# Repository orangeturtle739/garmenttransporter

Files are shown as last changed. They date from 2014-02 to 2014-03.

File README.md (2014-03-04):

garmenttransporter
==================
This project is my entry for the Hack the Arduino Robot competition (http://www.robotchallenge.org/competition/).

In June 2012, I build an automatic shirt-folding robot. In January 2014, I entered the Hack the Arduino Robot competition (http://www.robotchallenge.org/competition/) to try and win a free Arduino Robot. For the competition, I submitted the following paragraph describing what I would do if I won the robot:
“A couple of years ago, I built an Arduino-powered shirt-folding machine which folds clothes. Using the Arduino robot from the RobotChallenge, I will build a device to remove folded clothes from the machine and to stack them. My idea is special because it will involve two Arduinos (the Arduino Uno in the shirt folder, and the Arduino robot) which will have to communicate, and because it will be very useful. The robot will solve the real life problem of laundry folding by making the task easier and faster and by doing so nicely; the robot will use a custom-designed gripper to transport garments while keeping them perfectly folded.”
I won the robot and am now implementing my project.

The purpose of the project is to create an automatic shirt-stacking robot to go with the automatic shirt folding robot that I already have. The shirt stacking robot picks up a shirt from the shirt folder and then places the shirt into a pile.

This git repository contains all of my files for both the original shirt-folding robot along with the files for the shirt-stacking robot.

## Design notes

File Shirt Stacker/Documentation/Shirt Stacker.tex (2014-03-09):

\documentclass[12pt,letterpaper]{article}
\usepackage[utf8]{inputenc}
\usepackage{amsmath}
\usepackage{amsfonts}
\usepackage{amssymb}
\usepackage{graphicx}
\usepackage{hyperref}
\usepackage[space]{grffile}
\graphicspath{{/Users/jacob/Documents/My Stuff/Arduino/garmenttransporter/Shirt Stacker/Design/Images/}}

\title{Shirt Stacker}
\author{}
\date{}

\begin{document}
\maketitle
\section{Introduction}
This document describes the shirt-stacking machine which I built. The shirt-stacking machine is capable of picking up shirts from my shirt folder and stacking them. The machine is controlled by an Arduino Robot. All files for the shirt stacker can be found at \url{https://github.com/orangeturtle739/garmenttransporter/tree/master/Shirt\%20Stacker}.

\section{Design}
The shirt stacker consists of a rotating turntable and a spatula. The stacker picks up the shirt on the spatula, rotates and then drops the shirt. The spatula moves up and down using linear bearings. Figure \ref{topview} shows a rendering of the shirt stacker.

A SketchUp model of the shirt folder can be found at \url{https://github.com/orangeturtle739/garmenttransporter/blob/master/Shirt\%20Stacker/Design/Actual%20Design.skp}.

\subsection{Mechanics}
\subsubsection{Rotating}
The rotation is powered by the Arduino Robot's left wheel. The wheel rotates on a rubber track to rotate the shirt stacker. The turntable itself rotates on a lazy susan bearing. The Arduino Robot is attached to the rotating section with a wooden arm. Fiqure \ref{crossection} shows the mechanics.

\subsubsection{Lifting}
The lifting is powered by the Arduino Robot's right wheel. The wheel is attached to a wooden dowel which is attached to a string. When the wheel turns, the string winds up on the dowel. The spool and wheel connection are shown in figure \ref{spool}. The string then passes through a setup consisting of 9 pulleys. The pulleys are visible in figure \ref{pulleys}. This setup lifts the carriage that contains the spatula.

The carriage moves up and down on two linear bearings. Figure \ref{linearbearings} shows the bearings.

\subsubsection{Dumping}
Once the shirt folder has lifted the shirt and rotated to the proper location, the shirt folder drops the shirt. It does this by rotating the spatula. The spatula is attached to a wooden dowel which goes through a bearing. Along the diameter of the flat side of the dowel sticking out of the bearing, there are two nails, both very close to the edge. Figure \ref{nails} shows the location of the nails. Both nails are a attached to a piece of elastic to make the spatula self-righting. One nail is a attached to a string. The other end of the string is tied onto a screw eye on the base of the rotating platform. When the spatula reaches a specific height, this piece of string causes it to rotate. Once the robot lowers the spatula, the elastic makes it level again. This is shown in figure \ref{dumping}.

\section{Parts}
For the lazy susan bearing, I used this part: \url{http://www.amazon.com/gp/product/B00004YOKA/ref=oh_details_o02_s01_i03?ie=UTF8&psc=1}. For the linear bearings, I used these bearings: \url{http://www.amazon.com/gp/product/B00CGR8WUU/ref=oh_details_o03_s00_i01?ie=UTF8&psc=1}. I put the bearings on these shafts: \url{http://www.amazon.com/gp/product/B002BBJ0CA/ref=oh_details_o02_s00_i01?ie=UTF8&psc=1}. I held the shafts in place with these parts: \url{http://www.amazon.com/gp/product/B00C4PBMMY/ref=oh_details_o03_s00_i00?ie=UTF8&psc=1}.

\section{Use}
To use the shirt stacker, install the program which can be found at \url{https://github.com/orangeturtle739/garmenttransporter/blob/master/Shirt\%20Stacker/Code/Code.ino}. After installing the program, turn the Arduino Robot on. Use the Arduino Robot's buttons to control where the shirt stacker will place the shirt. After a button has been pressed, the robot will wait 14 seconds. Then, it will lift the shirt, rotate and then drop the shirt. 

\begin{figure}[ht]
  \centering
    
    \caption{Top view of shirt stacker.}
    \label{topview}
\end{figure}
\begin{figure}[ht]
  \centering
    
    \caption{Cross-sectional view of the shirt stacker.}
    \label{crossection}
\end{figure}
\begin{figure}[ht]
  \centering
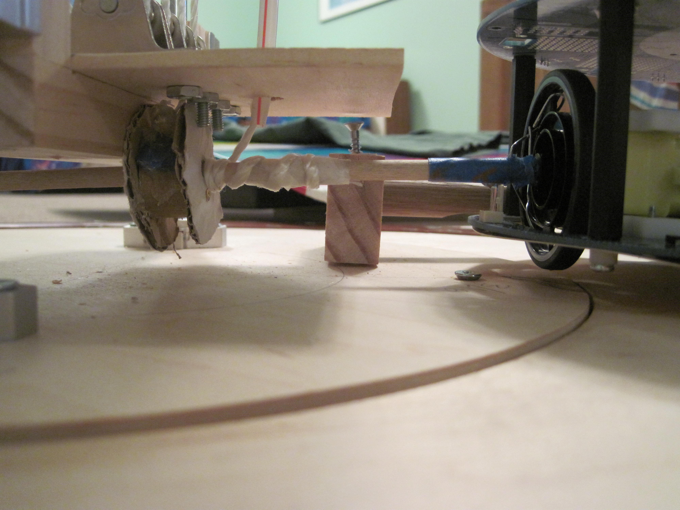
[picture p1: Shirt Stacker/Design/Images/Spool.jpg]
    
    \caption{The spool connected to the right wheel.}
    \label{spool}
\end{figure}
\begin{figure}[ht]
  \centering
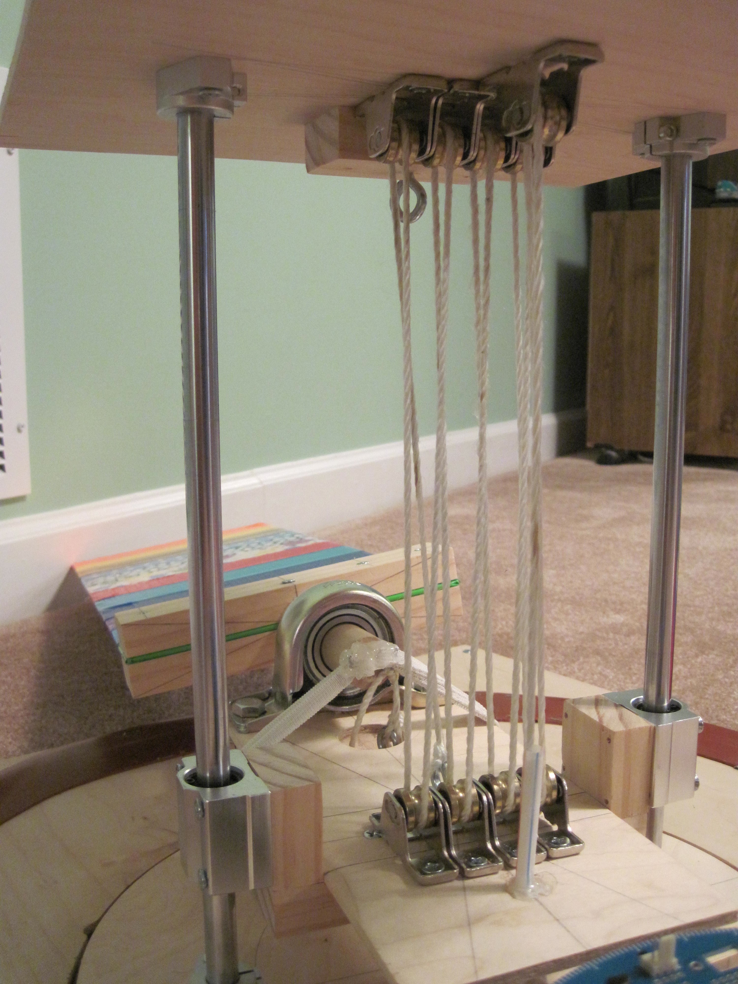
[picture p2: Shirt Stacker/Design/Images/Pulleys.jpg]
    
    \caption{The pulleys on the shirt stacker.}
    \label{pulleys}
\end{figure}
\begin{figure}[ht]
  \centering
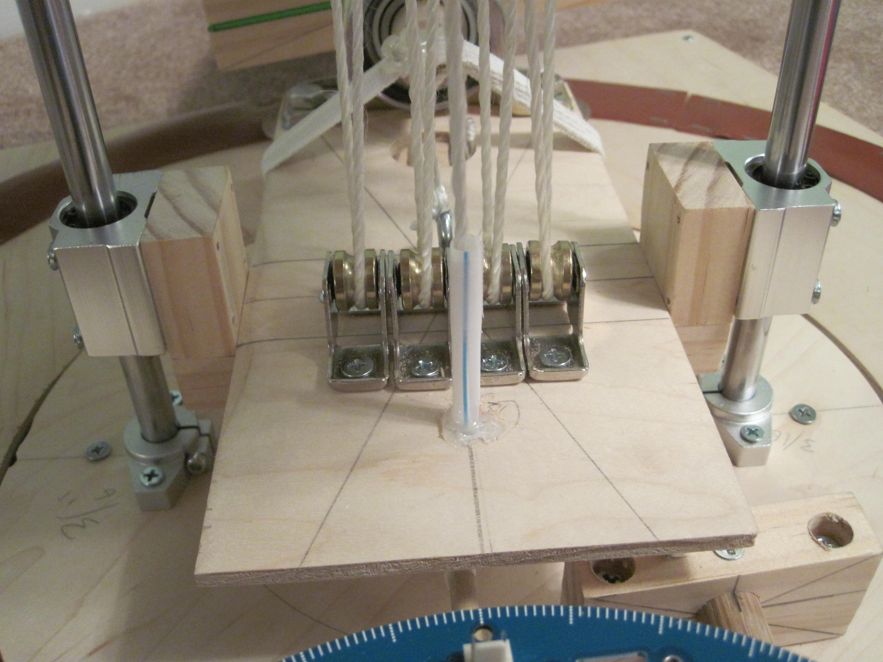
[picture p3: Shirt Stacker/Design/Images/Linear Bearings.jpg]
    
    \caption{The linear bearings.}
    \label{linearbearings}
\end{figure}
\begin{figure}[ht]
  \centering
    
    \caption{The location of the nails in the end of the dowel.}
    \label{nails}
\end{figure}
\begin{figure}[ht]
  \centering
3    
    \caption{The dumping mechanics.}
    \label{dumping}
\end{figure}
\end{document}

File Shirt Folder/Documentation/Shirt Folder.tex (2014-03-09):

\documentclass[12pt,letterpaper]{article}
\usepackage[utf8]{inputenc}
\usepackage{amsmath}
\usepackage{amsfonts}
\usepackage{amssymb}
\usepackage{graphicx}
\usepackage{hyperref}
\usepackage[space]{grffile}
\graphicspath{{/Users/jacob/Documents/My Stuff/Arduino/Shirt Folder/Shirt Folder/Design/Images/}}

\title{Shirt Folder}
\author{}
\date{}

\begin{document}
\maketitle
\section{Introduction}
This document describes the shirt-folding machine which I built. The shirt-folding machine is capable of folding most garments including shirts, shorts and pants. All files for the shirt folder can be found at \url{https://github.com/orangeturtle739/garmenttransporter/tree/master/Shirt\%20Folder}.

\section{Design}
The shirt folder consists of three flaps. Each flap is connected to a servo which can rotate the flap. Figure \ref{topview} shows a rendering of the shirt folder. Each of the flaps fold inward as shown in figure \ref{opentopview}.

The servos are connected to the flaps with a linkage consisting of wooden arms. Figure \ref{servolinkage} shows the linkage. When the button is hit, the shirt folder folds a shirt.

A SketchUp model of the shirt folder can be found at \url{https://github.com/orangeturtle739/garmenttransporter/blob/master/Shirt\%20Folder/Design/Shirt\%20Folder.skp}.

\section{Electronics}
Figure \ref{schematic} shows a schematic of the shirt folder's circuit. Every servo has its own 6V power supply and the Arduino Uno has a 9V power supply. All of the power supplies have their own switches and all of the grounds are connected together.

\section{Parts}
I used TowerPro 9805BB servos because they are able to provide lots of torque. For the main switch (labeled "Button" in figure \ref{topview}), I used a round push-on/push-off switch. For the Arduino switch and the servo switches, I used rocker switches.

\section{Use}
To use to shirt folder, install the program which can be found at \url{https://github.com/orangeturtle739/garmenttransporter/blob/master/Shirt\%20Folder/Shirt_Folder/Shirt_Folder.ino}. After installing the program, turn the Arduino on. Press the main switch twice (turn it on then off again) to initialize the servos. Then, place the shirt onto the shirt folder and press the main switch. Once the bottom flap has be activated, the folder will wait. Pull the shirt onto the bottom flap and press the main switch again. This will cause the bottom flap to rotate one more time which will complete the shirt folding.

\begin{figure}[ht]
  \centering
    
    \caption{Top view of shirt folder.}
    \label{topview}
\end{figure}
\begin{figure}[ht]
  \centering
    
    \caption{Top view of shirt folder with one of the side flaps rotated.}
    \label{opentopview}
\end{figure}
\begin{figure}[ht]
  \centering
    
    \caption{The servo linkage.}
    \label{servolinkage}
\end{figure}
\begin{figure}[ht]
  \centering
    
    \caption{The schematic.}
    \label{schematic}
\end{figure}
\end{document}

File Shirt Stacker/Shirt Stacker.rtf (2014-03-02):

The shirt stacker works by lifting the shirt with a spatula, rotating to the specified location, and depositing the shirt in a pile.

The shirt is first folded by a shirt folding machine. The shirt folding machine uses three servo motors and is controlled by Arduino Uno.

Once the shirt is folded, the shirt stacker lifts the shirt into the air and rotates. Before folding the shirt, the desired location for the shirt is selected via the buttons on the Arduino Robot. I hope to replace this clumsy mechanism with a potentiometer located next the the glowing red button that activates the shirt folder. Also, I hope to add a servo motor to control the spatula such that when the shirt arrives at its destination, the robot can automatically flip the spatula over.

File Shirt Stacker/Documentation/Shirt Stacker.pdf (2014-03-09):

# Shirt Stacker

## 1 Introduction

This document describes the shirt-stacking machine which I built. The shirt-stacking machine is capable of picking up shirts from my shirt folder and stacking them. All files for the shirt stacker can be found at https://github.com/orangeturtle739/garmenttransporter/tree/master/Shirt%20stacker. (https://github.com/orangeturtle739/garmenttransporter/tree/master/Shirt%20stacker)

## 2 Design

The shirt stacker consists of a rotating turntable and a spatula. The stacker picks up the shirt on the spatula, rotates and then drops the shirt. The spatula moves up and down using linear bearings. Figure 1 shows a rendering of the shirt stacker.
A SketchUp model of the shirt folder can be found at https://github.com/orangeturtle739/garmenttransporter/blob/master/Shirt%20Folder/Design/Shirt%20Folder.skp. (https://github.com/orangeturtle739/garmenttransporter/blob/master/Shirt%20Folder/Design/Shirt%20Folder.skp)

## 3 Electronics

Figure ?? shows a schematic of the shirt folder’s circuit. Every servo has its own 6V power supply and the Arduino Uno has a 9V power supply. All of the power supplies have their own switches and all of the grounds are connected together.

1

## 4 Parts

I used TowerPro 9805BB servos because they are able to provide lots of torque. For the main switch (labeled ”Button” in figure 1), I used a round push-on/push-off switch. For the Arduino switch and the servo switches, I used rocker switches.

## 5 Use

To use to shirt folder, install the program which can be found at https://github.com/orangeturtle739/garmenttransporter/blob/master/Shirt%20Folder/Shirt_Folder/Shirt_Folder.ino. (https://github.com/orangeturtle739/garmenttransporter/blob/master/Shirt%20Folder/Shirt_Folder/Shirt_Folder.ino) After installing the program, turn the Arduino on. Press the main switch twice (turn it on then off again) to initialize the servos. Then, place the shirt onto the shirt folder and press the main switch. Once the bottom flap has be activated, the folder will wait. Pull the shirt onto the bottom flap and press the main switch again. This will cause the bottom flap to rotate one more time which will complete the shirt folding.

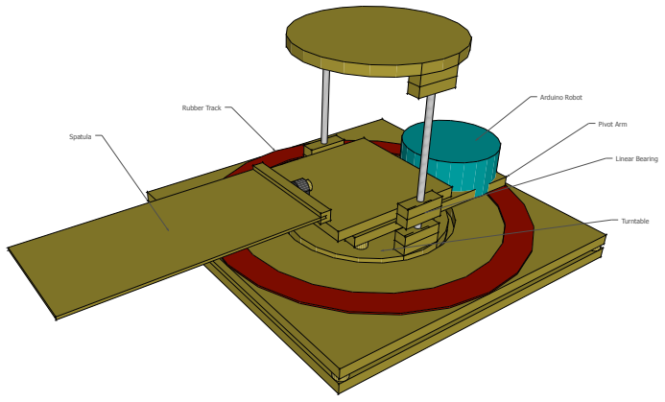
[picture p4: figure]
Spatula; Arduino Robot; Turntable; Linear Bearing; Pivot Arm; Rubber Track

Figure 1: Top view of shirt folder.

2

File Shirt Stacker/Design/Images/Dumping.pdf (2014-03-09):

Start | End

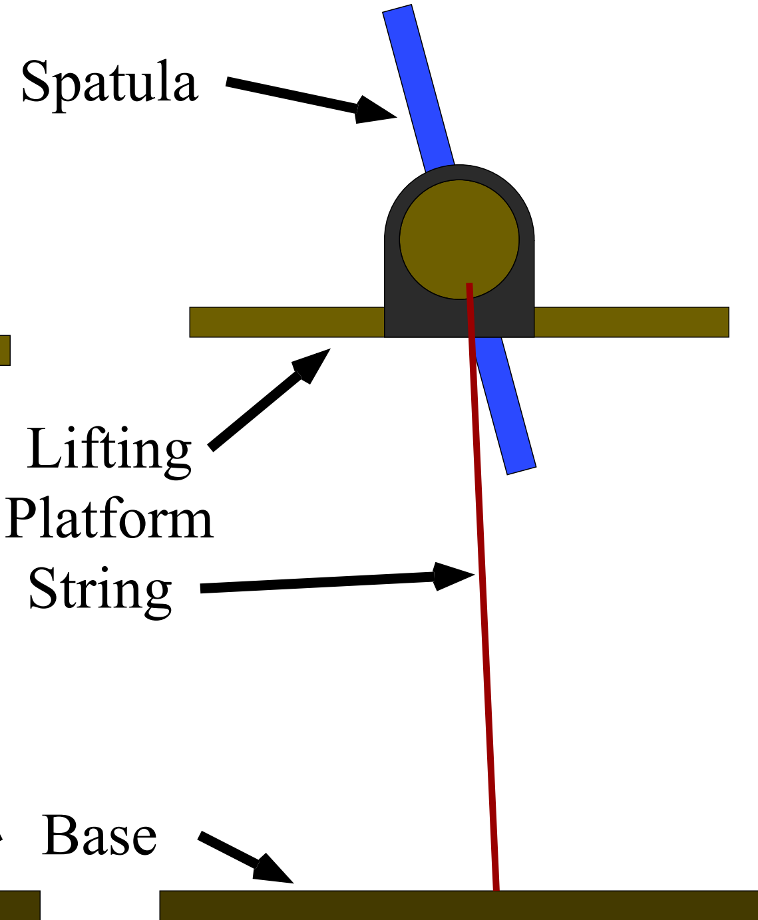
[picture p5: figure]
Spatula; Lifting Platform String; Base
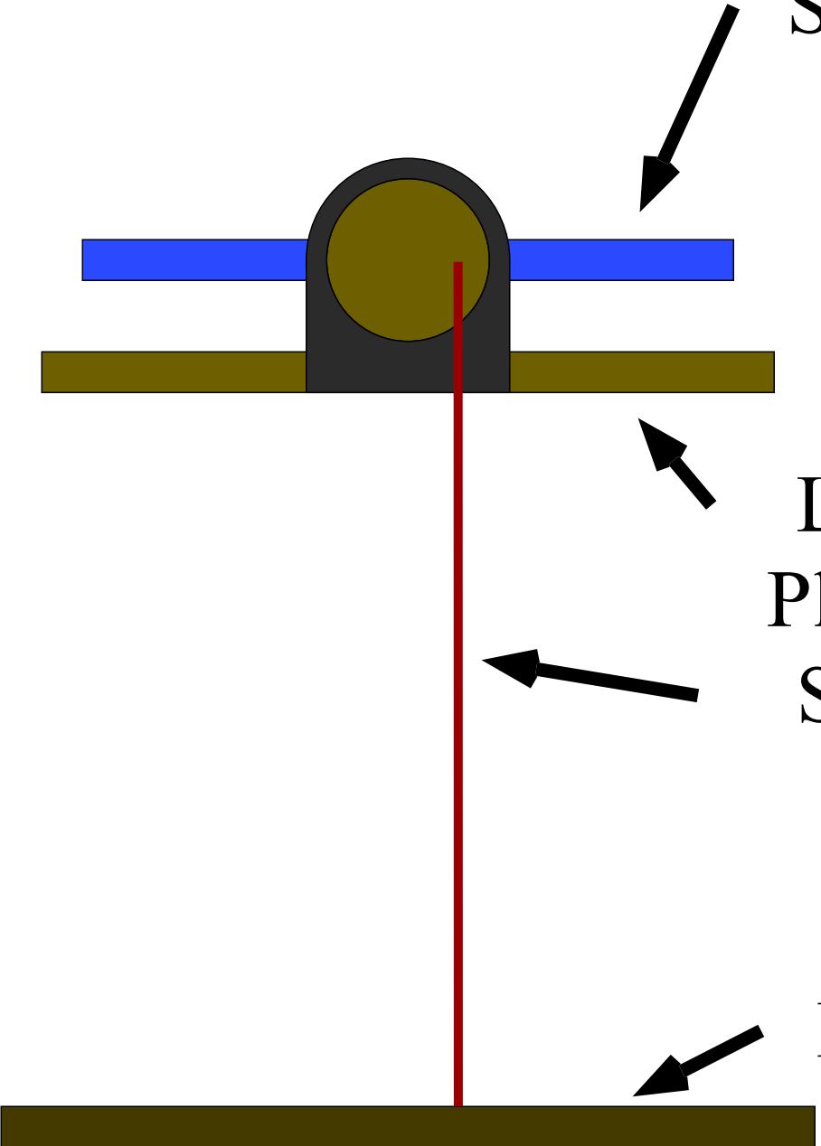
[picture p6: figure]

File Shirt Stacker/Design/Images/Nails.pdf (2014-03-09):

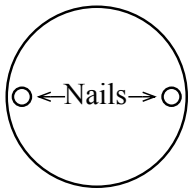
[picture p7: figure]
Nails

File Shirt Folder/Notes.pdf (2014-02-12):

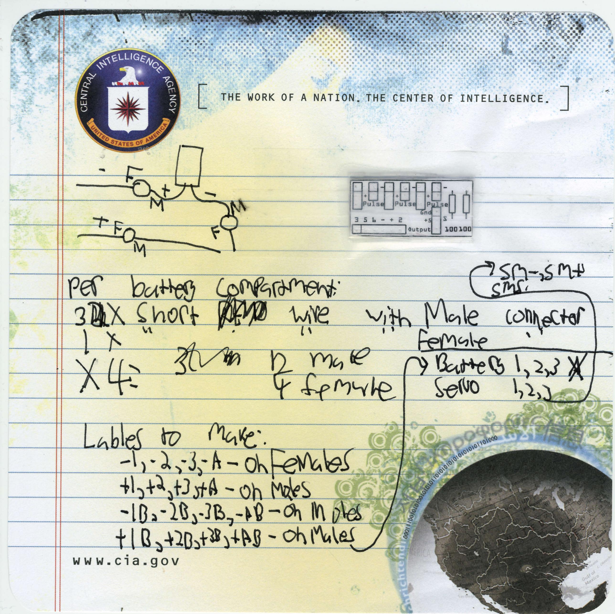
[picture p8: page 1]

THE WORK OF A NATION. THE CENTER OF INTELLIGENCE.

# Qffi'

tF | T-w-t | @l-?ol Sc$o

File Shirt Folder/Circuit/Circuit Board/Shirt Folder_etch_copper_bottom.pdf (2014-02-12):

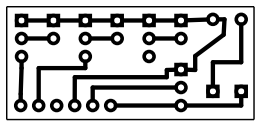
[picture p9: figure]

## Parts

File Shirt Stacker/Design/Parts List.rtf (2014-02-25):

Shirt Stacker Parts List
Part | Quantity
48” x 48” x 3/4” plywood | 1
24” x 1” diameter dowel | 1
48” x 1” x 3/4” wood | 2
1 1/4 inch long wood screws | 1 box
5/8 inch long wood screws | 1 box
1 inch long #8 self-tapping sheet metal screws | 1 box
Wood glue | 1 large container
2 inch long wood screws | 1 box
Dial 1" Pillow Block Bearing | 1
3mm diameter bolt, 40 mm length | 2
3mm nut | 2
3mm washer | 6
Screws and hardware for pillow block | 1

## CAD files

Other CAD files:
Shirt Folder/Design/Shirt Folder.skp
Shirt Folder/Design/Shirt Folder~.skp
Shirt Stacker/Design/Actual Design.skp
Shirt Stacker/Design/Actual Design~.skp
Shirt Stacker/Plans/Cutout Plans.skp
Shirt Stacker/Plans/Cutout Plans~.skp
Shirt Stacker/Stacker SketchUp/Stacker.skp
Shirt Stacker/Stacker SketchUp/Stacker~.skp

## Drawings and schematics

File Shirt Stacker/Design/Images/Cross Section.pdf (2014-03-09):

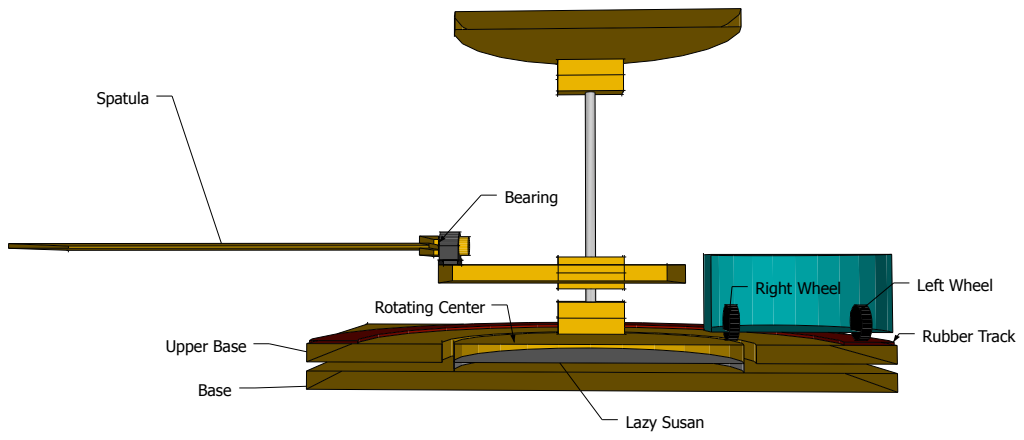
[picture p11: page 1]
Spatula; Bearing; Base; Upper Base; Rotating Center; Lazy Susan; Right Wheel; Left Wheel; Rubber Track

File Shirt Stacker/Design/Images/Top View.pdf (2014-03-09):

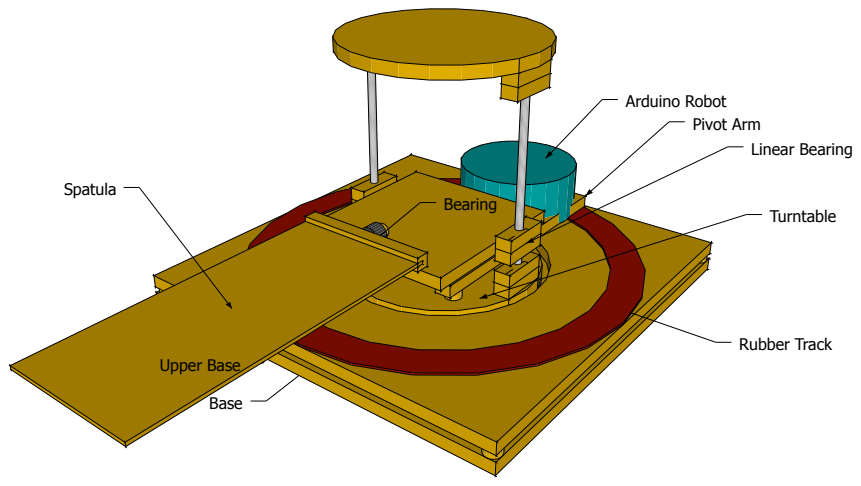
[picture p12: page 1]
Spatula; Arduino Robot; Turntable; Linear Bearing; Pivot Arm; Bearing; Base; Upper Base; Rubber Track

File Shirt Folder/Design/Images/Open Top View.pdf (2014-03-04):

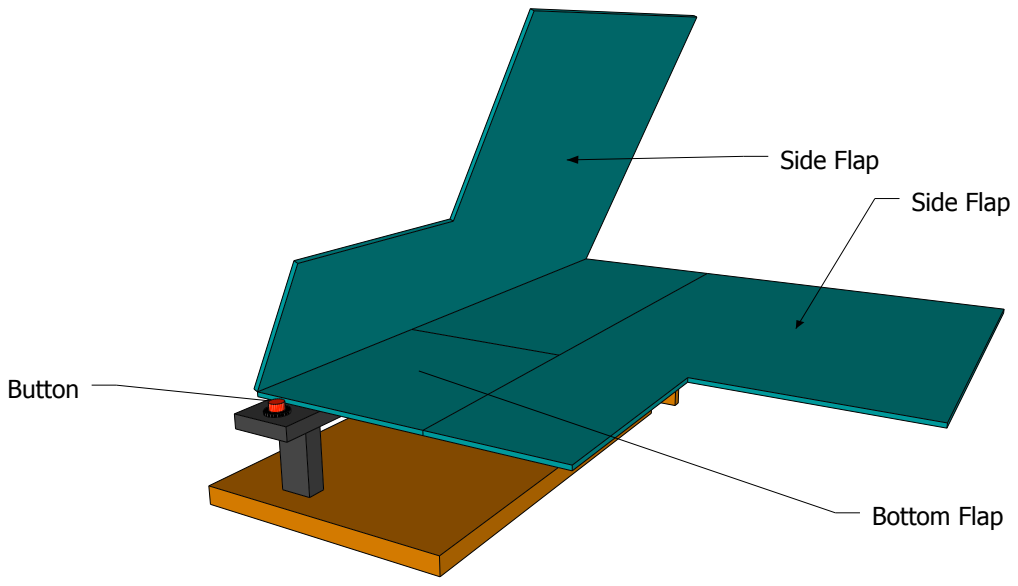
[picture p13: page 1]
Side Flap; Bottom Flap; Button

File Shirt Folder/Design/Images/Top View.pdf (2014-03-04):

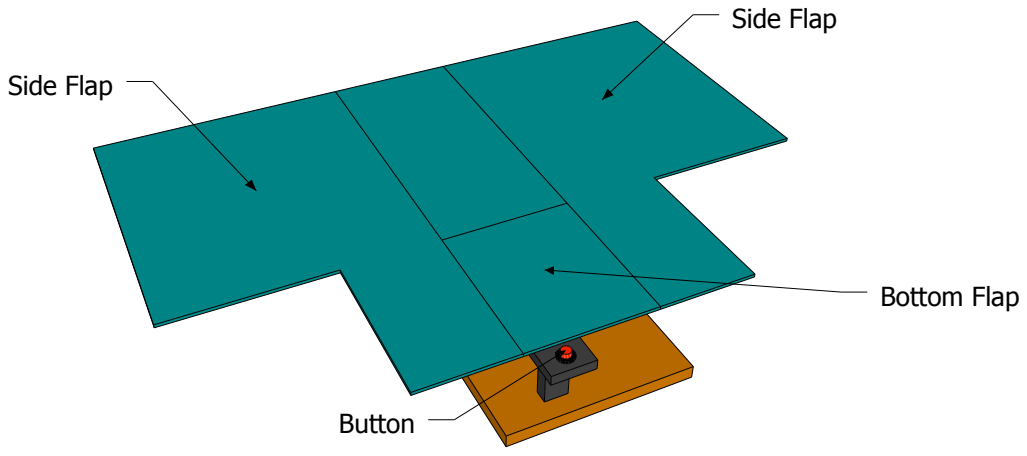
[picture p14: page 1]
Side Flap; Bottom Flap; Button

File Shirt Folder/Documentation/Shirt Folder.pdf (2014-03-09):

# Shirt Folder

## 1 Introduction

This document describes the shirt-folding machine which I built. The shirt-folding machine is capable of folding most garments including shirts, shorts and pants. All files for the shirt folder can be found at https://github.com/orangeturtle739/garmenttransporter/tree/master/Shirt%20Folder. (https://github.com/orangeturtle739/garmenttransporter/tree/master/Shirt%20Folder)

## 2 Design

The shirt folder consists of three flaps. Each flap is connected to a servo which can rotate the flap. Figure 1 shows a rendering of the shirt folder. Each of the flaps fold inward as shown in figure 2.
The servos are connected to the flaps with a linkage consisting of wooden arms. Figure 3 shows the linkage. When the button is hit, the shirt folder folds a shirt.
A SketchUp model of the shirt folder can be found at https://github.com/orangeturtle739/garmenttransporter/blob/master/Shirt%20Folder/Design/Shirt%20Folder.skp. (https://github.com/orangeturtle739/garmenttransporter/blob/master/Shirt%20Folder/Design/Shirt%20Folder.skp)

## 3 Electronics

Figure 4 shows a schematic of the shirt folder’s circuit. Every servo has its own 6V power supply and the Arduino Uno has a 9V power supply. All of the power supplies have their own switches and all of the grounds are connected together.

1

## 4 Parts

I used TowerPro 9805BB servos because they are able to provide lots of torque. For the main switch (labeled ”Button” in figure 1), I used a round push-on/push-off switch. For the Arduino switch and the servo switches, I used rocker switches.

## 5 Use

To use to shirt folder, install the program which can be found at https://github.com/orangeturtle739/garmenttransporter/blob/master/Shirt%20Folder/Shirt_Folder/Shirt_Folder.ino. (https://github.com/orangeturtle739/garmenttransporter/blob/master/Shirt%20Folder/Shirt_Folder/Shirt_Folder.ino) After installing the program, turn the Arduino on. Press the main switch twice (turn it on then off again) to initialize the servos. Then, place the shirt onto the shirt folder and press the main switch. Once the bottom flap has be activated, the folder will wait. Pull the shirt onto the bottom flap and press the main switch again. This will cause the bottom flap to rotate one more time which will complete the shirt folding.

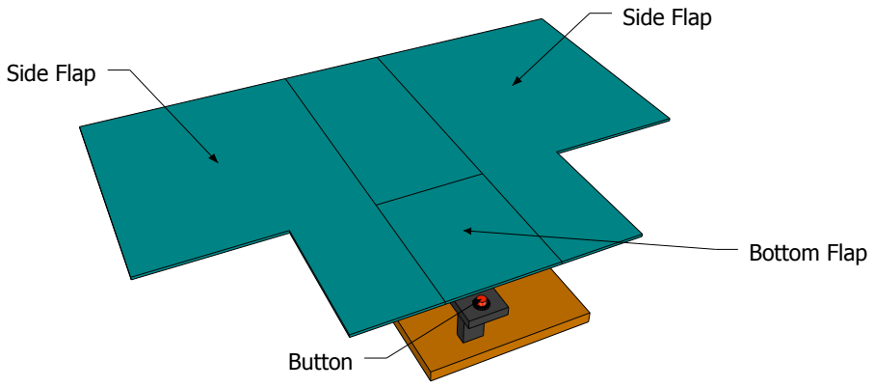
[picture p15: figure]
Side Flap; Bottom Flap; Button

Figure 1: Top view of shirt folder.

2

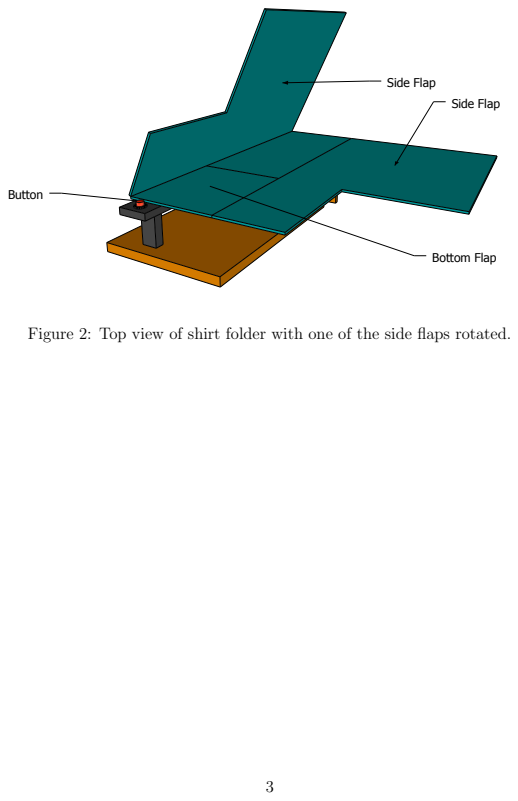
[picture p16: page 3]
Side Flap; Bottom Flap; Button

Figure 2: Top view of shirt folder with one of the side flaps rotated.

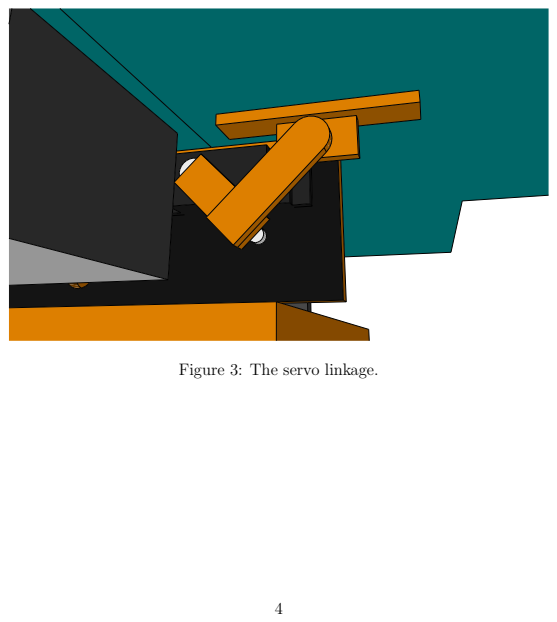
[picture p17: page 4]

Figure 3: The servo linkage.

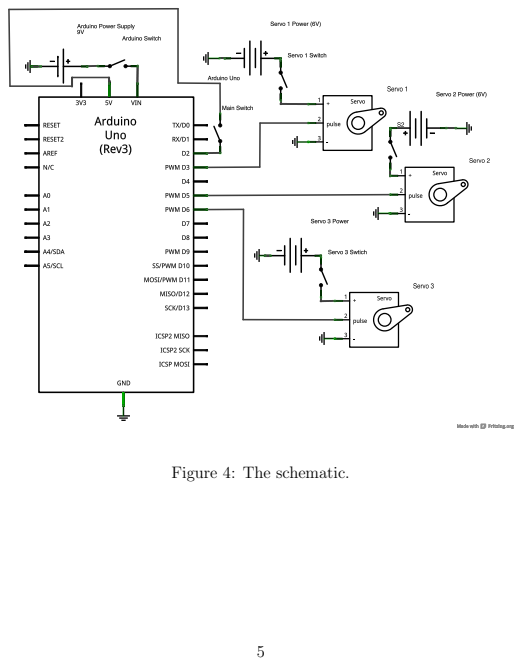
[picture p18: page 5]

Figure 4: The schematic.

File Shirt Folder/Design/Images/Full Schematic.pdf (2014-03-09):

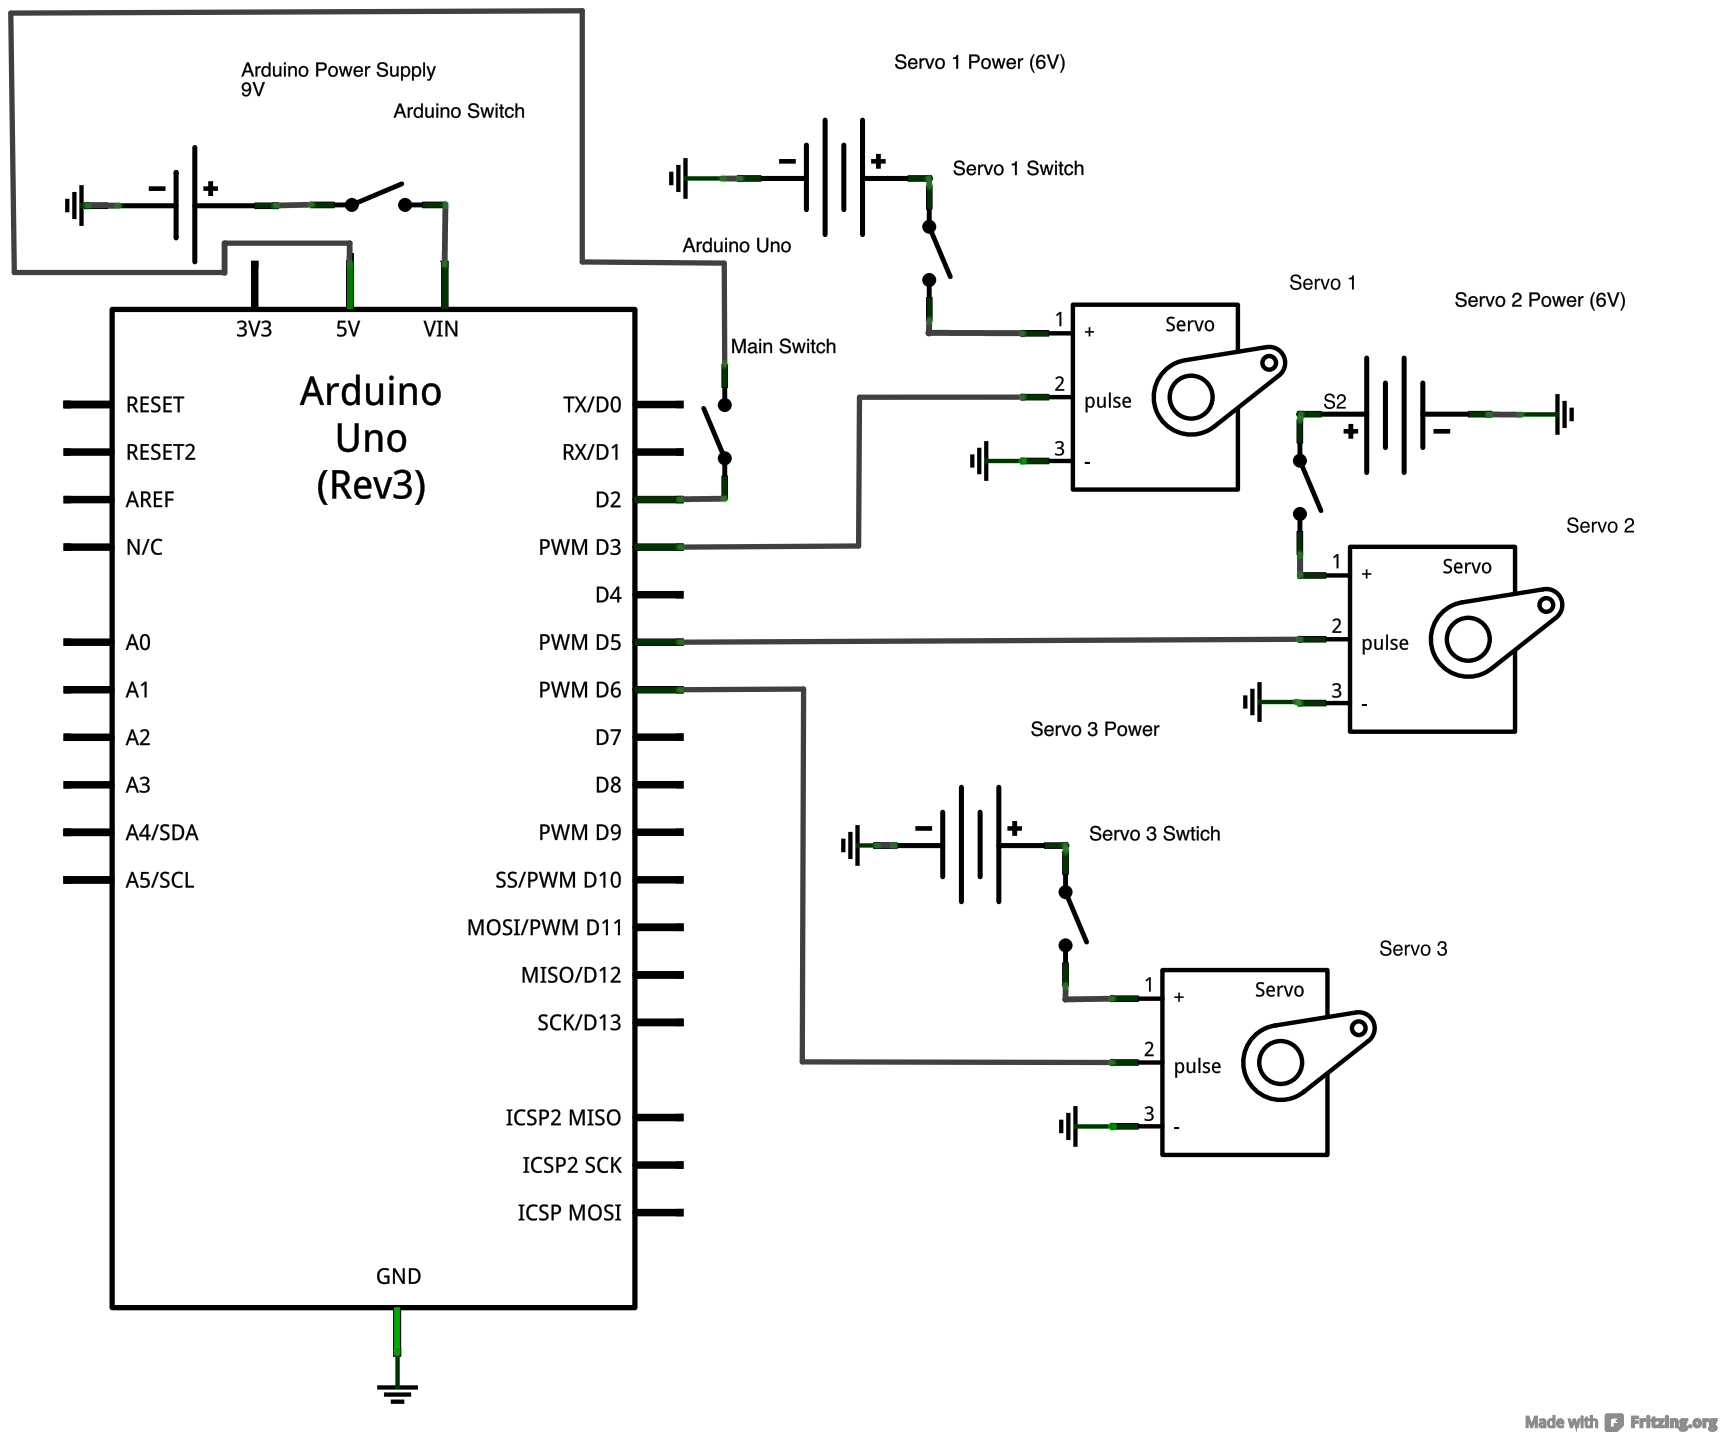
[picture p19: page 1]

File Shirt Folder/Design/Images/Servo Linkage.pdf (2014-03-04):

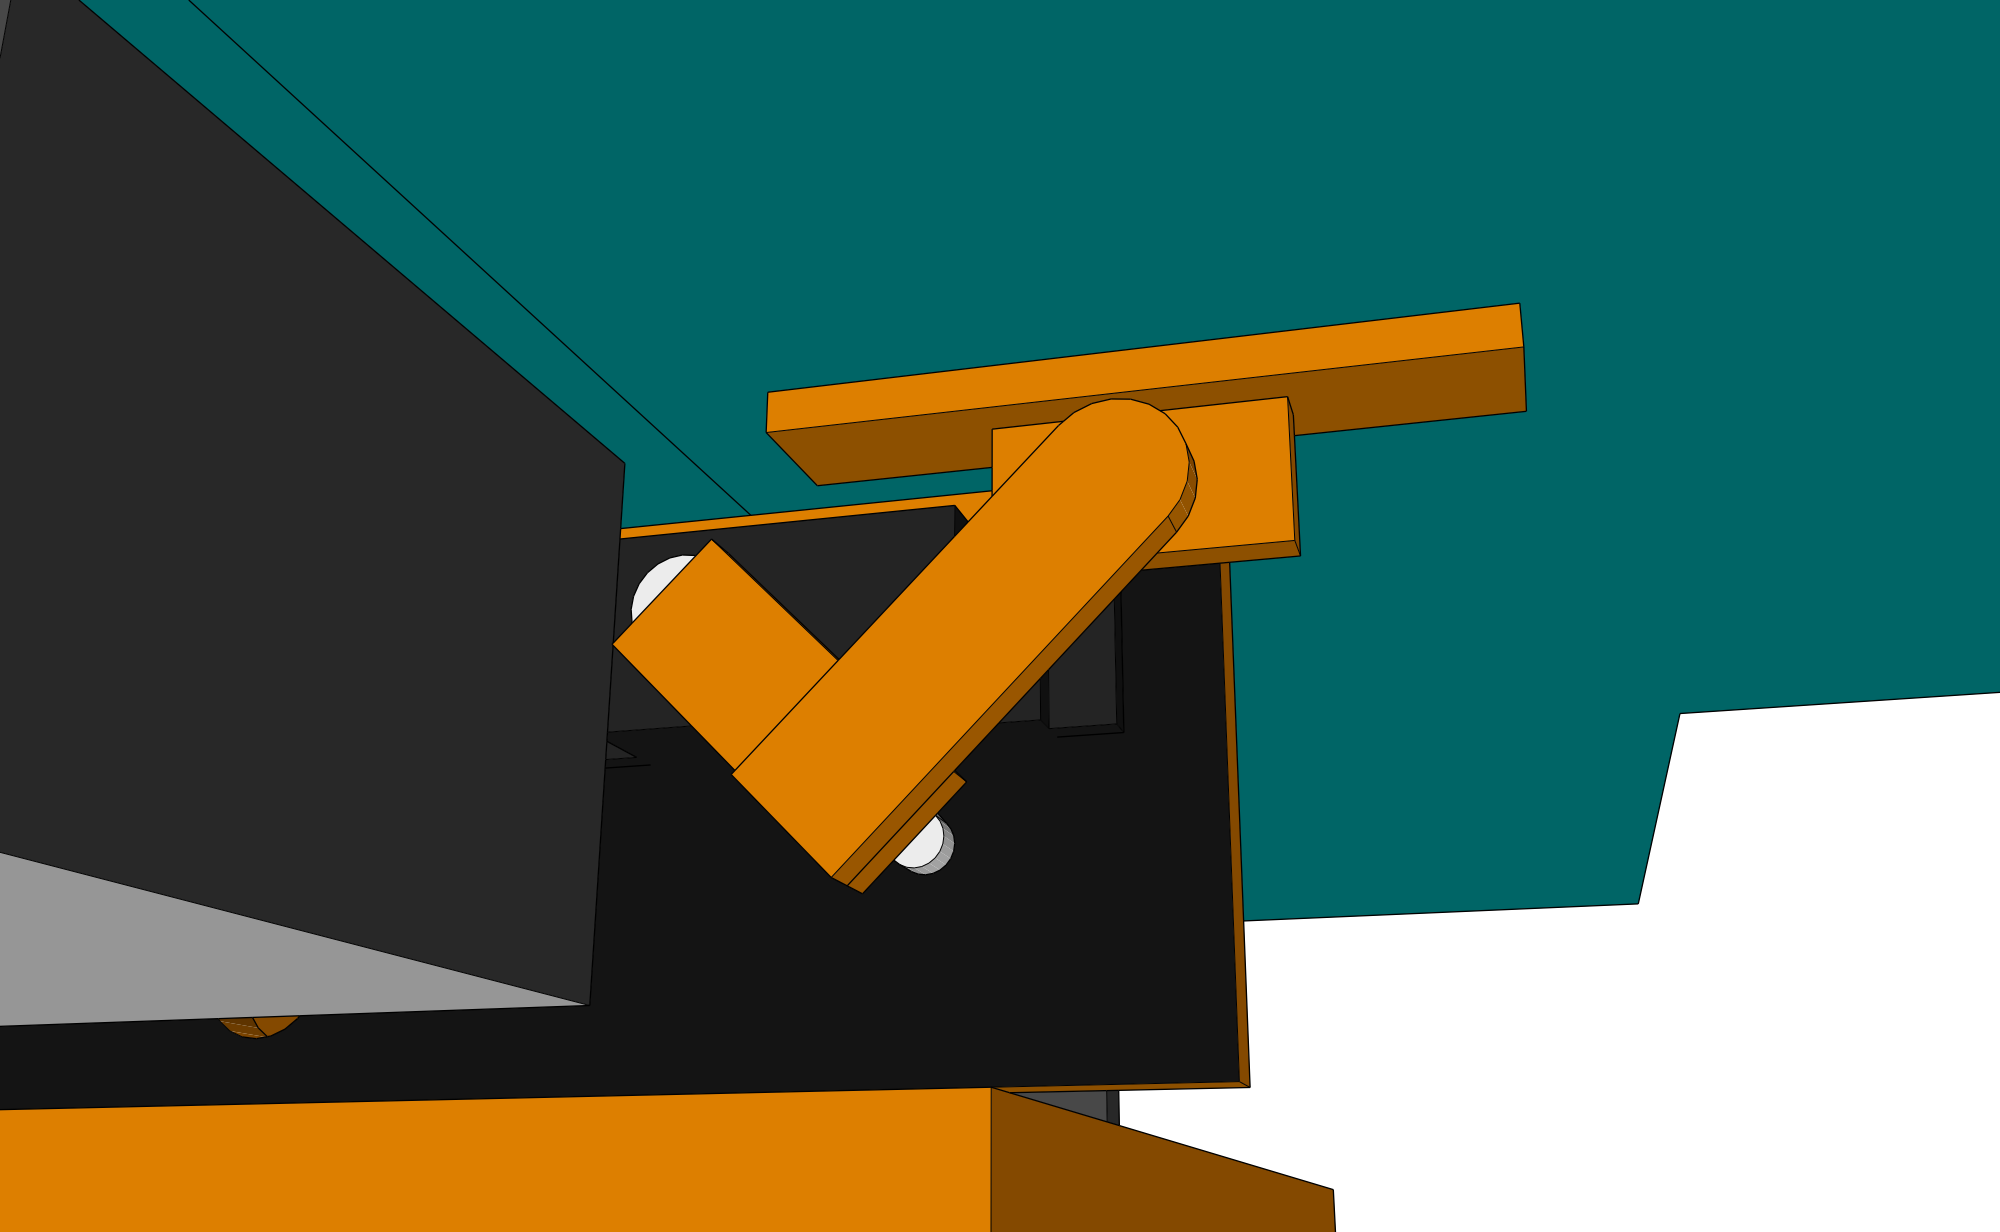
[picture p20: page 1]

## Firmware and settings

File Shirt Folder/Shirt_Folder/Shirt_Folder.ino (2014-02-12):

#include <Servo.h>
//Define servo and switch ports.
#define servo1_port 3
#define servo2_port 5
#define servo3_port 6
#define switch_port 2
//Define the zero positions for the servos.
#define servo1_inital_position 155
#define servo2_inital_position 50
#define servo3_inital_position 2
//Define the 90 degree position for the servos.
#define servo1_90_position 60
#define servo2_90_position 130
#define servo3_90_position 120
//Define the number which needs to be added to the 90 degree value in order the reach the final location.
#define servo1_90_to_final -20
#define servo2_90_to_final 20
#define servo3_90_to_final 30
//Calculate the final positions of all the servos.
#define servo1_final_position servo1_90_to_final + servo1_90_position
#define servo2_final_position servo2_90_to_final + servo2_90_position
#define servo3_final_position servo3_90_to_final + servo3_90_position
//Define all other constants
#define delay_after_movement 1500
Servo servo1;
Servo servo2;
Servo servo3;
void setup(){
  pinMode(switch_port,INPUT);
  servo1.attach(servo1_port);
  servo2.attach(servo2_port);
  servo3.attach(servo3_port);
  relaxServos();
  
  //Serial.begin(9600);
  //Serial.println(digitalRead(switch_port));
  if(digitalRead(switch_port)==HIGH){
    while(digitalRead(switch_port)==HIGH);
    delay(200);
  }else if(digitalRead(switch_port)==LOW){
    while(digitalRead(switch_port)==LOW);
    delay(200);
    while(digitalRead(switch_port)==HIGH);
    delay(200);
  }
  resetServos(true);
  
}
void loop(){
  
  if(digitalRead(switch_port)==HIGH){
    
    sendServoToPosition(1,servo1_final_position,true);
    sendServoToPosition(1,servo1_inital_position,false);
    sendServoToPosition(3,servo3_final_position,true);
    sendServoToPosition(3,servo3_inital_position,false);
    sendServoToPosition(1,servo1_final_position,true);
    sendServoToPosition(1,servo1_inital_position,false);
    if(digitalRead(switch_port)==LOW){
      sendServoToPosition(3,servo3_final_position,true);
      sendServoToPosition(3,servo3_inital_position,false);
      while(digitalRead(switch_port)==LOW);
    }
    delay(100);
    sendServoToPosition(2,servo2_final_position,true);
    sendServoToPosition(2,servo2_inital_position,true);
    while(digitalRead(switch_port)==HIGH);
    delay(50);
    sendServoToPosition(2,servo2_final_position,true);
    sendServoToPosition(2,servo2_inital_position,true);
    relaxServos();
 }
  
}
void resetServos(boolean wait){
  servo1.write(servo1_inital_position);
  servo2.write(servo2_inital_position);
  servo3.write(servo3_inital_position);
  if(wait){
    delay(delay_after_movement);
    relaxServos();
  }
}
void relaxServos(){
  servo1.write(0);
  servo2.write(0);
  servo3.write(0);
}
void sendServoToPosition(int servoNum, int servoPosition, boolean wait){
  switch(servoNum){
    case 1:
      servo1.write(servoPosition);
      break;
    case 2:
      servo2.write(servoPosition);
      break;
    case 3:
      servo3.write(servoPosition);
      break;
  }
  if(wait)
    delay(delay_after_movement);
}

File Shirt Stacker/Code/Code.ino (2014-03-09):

#include <ArduinoRobot.h> 

void setup(){
  Robot.begin(); // initialize the library
  Robot.beginSpeaker();
  Robot.beginTFT();
}

void loop(){

  //Print
  Robot.debugPrint(111);

  //Get inpout
  int button = BUTTON_NONE;
  while(button==BUTTON_NONE) {
    button = Robot.keyboardRead();
  }
  Robot.beep(BEEP_SIMPLE);

  //Raise the shirt
  delay(14000);
  Robot.motorsWrite(0,255);
  delay(12000);
  Robot.motorsWrite(0,0);

  int pos;
  if( button == BUTTON_DOWN){
    pos = 3;
  } 
  else if( button == BUTTON_RIGHT){
    pos = 2;
  } 
  else{
    pos = 1;
  }

  //Print out the positon
  Robot.debugPrint(pos);

  //Go there
  rotateToPos(pos, -255);

  //Dump the shirt
  Robot.motorsWrite(0,255);
  delay(4000);

  //Go back
  rotateToPos(pos,255);

  //Lower the tray
  Robot.motorsWrite(0,-255);
  delay(7500);

  //Stop everything
  Robot.motorsWrite(0,0);
}

void rotateToPos(double spot, int power) {
  Robot.motorsWrite(power,0);
  delay(spot*1000);
  Robot.motorsWrite(0,0);
}

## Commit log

2014-02-12 Initial commit.
    [Shirt Folder 2.fzz, Shirt Folder 3.fzz, Shirt Folder.fzz]
2014-02-13 Put all the shirt folder files into a folder.
    [Shirt Folder 2.fzz, Shirt Folder 3.fzz, Shirt Folder.fzz]
2014-02-13 Create a SketchUp model of the shirt stacker.
    Make the first draft of the shirt stacker design. “Stacker.skp” is the
    real file; the others are support files created by SketchUp.
    [Stacker.skp, Stacker~.skp]
2014-02-13 Put the Arduino on the bottom of the design.
    Change the design of the stacker such that the Arduino can be on the
    bottom.
    [Stacker.skp, Stacker~.skp]
2014-02-13 Add the Arduino Robot to the design.
    [Stacker.skp, Stacker~.skp]
2014-02-14 Reposition the robot and remove a random pulley.
    Place the robot such that it will have an easier time rotating the
    device. Also, remove a random pulley.
    [Stacker.skp, Stacker~.skp]
2014-02-25 Add the final design.
    Add the final design files and a parts list.
    [Actual Design.skp, Actual Design~.skp, Cutout Plans.skp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]
2014-02-26 Reorganize files and add renderings.
    [Actual Design.skp, Actual Design~.skp]
2014-03-04 Added a SketchUp model of the shirt folder and some renderings.
    [Shirt Folder.skp, Shirt Folder~.skp]
2014-03-04 Changed the coloring the the stacker SketchUp model.
    [Actual Design.skp, Actual Design~.skp]
2014-03-09 Add lots of documentation and update code.
    [Complete Circuit.fzz, Shirt Folder 2.fzz, Shirt Folder 3.fzz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]
2014-03-09 Reorganize some files.
    [Actual Design.skp, Actual Design~.skp]
2014-03-09 Add more documentation.
    [Actual Design.skp, Actual Design~.skp]
